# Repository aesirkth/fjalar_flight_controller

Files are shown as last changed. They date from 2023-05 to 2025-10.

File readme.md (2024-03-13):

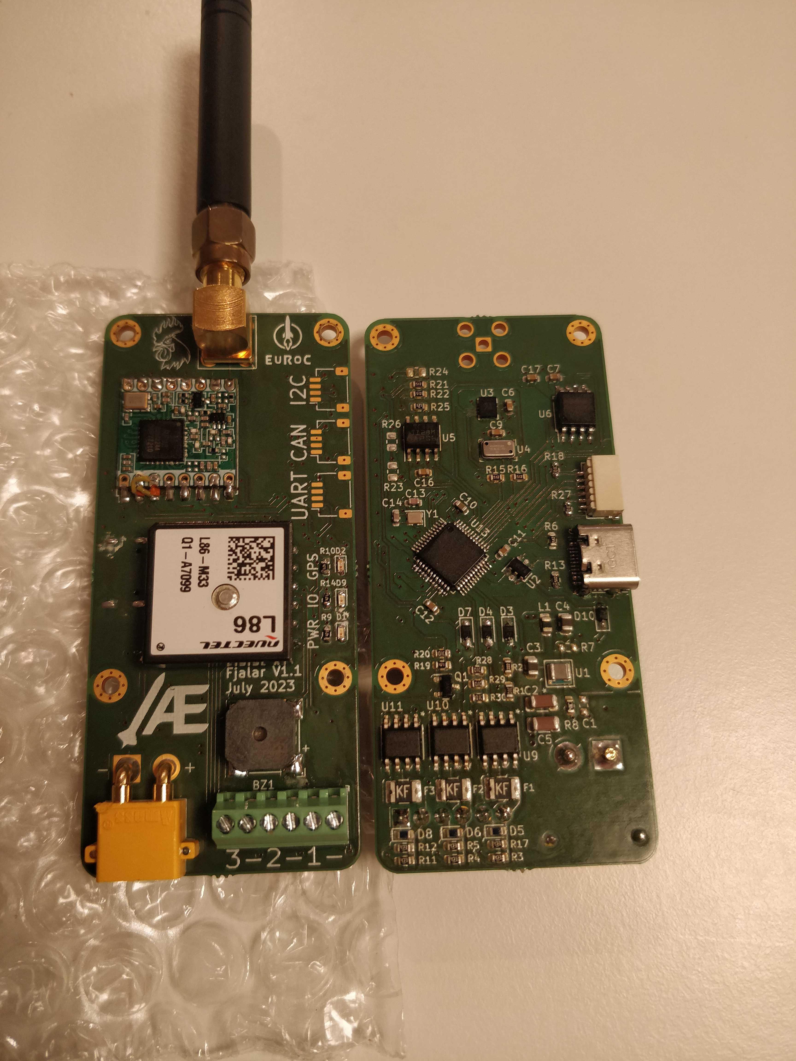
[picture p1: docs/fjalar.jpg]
fjalar


# Fjalar flight controller
Fjalar is a rooster in Jotunheim who heralds the advent of ragnarök, or in our case, apogee.

### features
1. 3 pyro channels
1. barometer
1. IMU
1. GPS
1. USB-C
1. flash memory
1. CAN, I2C, UART connectors
1. LoRa radio
1. continuity detection

### schematic
see [here](./design/euroc_controller.pdf)

### hardware
hopefully soon :)

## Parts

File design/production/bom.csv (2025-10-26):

Designator | Footprint | Quantity | Value | LCSC Part #
BZ1 | MagneticBuzzer_CUI_CMT-8504-100-SMT | 1 | CMT-8504-100
C1, C15, C2, C3, C8 | 0603 | 5 | 1u
C10, C11, C12 | 0603 | 3 | 4u7
C13, C14 | 0603 | 2 | 14p
C16, C17, C6, C7, C9 | 0603 | 5 | 0.1u
C18, C19 | 0603 | 2 | 10u
C20 | 0603 | 1 | 220n
C21, C4, C5 | 0603 | 3 | 100n
D1 | 0603 | 1 | power
D10 | D_SOD-323_HandSoldering | 1 | D_Small
D2 | 0603 | 1 | LED_FIX
D3, D4, D7 | D_SOD-323_HandSoldering | 3 | 3V
D5, D6, D8 | 0603 | 3 | 15V
D9 | 0603 | 1 | status
F1, F2, F3 | 1210 | 3 | Polyfuse
FB2, FB4 | 0805 | 2 | BLM18KG102SN1D
H1, H2, H3, H4 | MountingHole_2.2mm_M2_Pad_Via | 4 | MountingHole_Pad
IC1 | SOT-23-6_Handsoldering | 1 | LMR50410Y3
J1 | AMASS_XT30PW-M_1x02_P2.50mm_Horizontal | 1 | xt30
J2 | JST_GH_SM06B-GHS-TB_1x06-1MP_P1.25mm_Horizontal | 1 | jst gh 6
J3 | JST_GH_SM04B-GHS-TB_1x04-1MP_P1.25mm_Horizontal | 1 | jst gh 4
J6 | SMA_Amphenol_901-143_Horizontal | 1 | SMA
J7 | TerminalBlock_TE_282834-6_1x06_P2.54mm_Horizontal | 1 | Screw_Terminal_01x06
J8 | USB_C_Receptacle_Palconn_UTC16-G | 1 | USB_C_Receptacle_USB2.0
J9 | JST_SH_SM06B-SRSS-TB_1x06-1MP_P1.00mm_Horizontal | 1 | jst_sh 6
L2 | L_Wurth_WE-LQSH-3012 | 1 | 4.7u
Q1 | SOT-23 | 1 | MMBT3904
R1, R18, R20, R27, R28, R29, R30 | 0603 | 7 | 10k
R10, R14, R19, R9 | 0603 | 4 | 470
R11, R12, R17, R3, R4, R5 | 0603 | 6 | 3k
R13, R15, R16, R6 | 0603 | 4 | 5k1
R2 | 0603 | 1 | 2k2
R25 | 0603 | 1 | 120
SW1 | SW_SPST_B3U-1000P | 1 | SW_SPST
U10, U11, U9 | SOIC_050ASTR_STM | 3 | VN7050ASTR
U12 | HOPERF_RFM9XW_SMD | 1 | RFM98W-433S2
U13 | LQFP-48_7x7mm_P0.5mm | 1 | STM32U575CGTx
U2 | SOT-23-6 | 1 | USBLC6-2SC6
U3 | LGA-14_3x2.5mm_P0.5mm_LayoutBorder3x4y | 1 | LSM6DSO32
U4 | LGA-8_3x5mm_P1.25mm | 1 | MS5611-01BA
U5 | SOIC-8_3.9x4.9mm_P1.27mm | 1 | TCAN332
U6 | SOIC-8_5.23x5.23mm_P1.27mm | 1 | W25Q128JVS
U7 | LGA-12_2x2mm_P0.5mm | 1 | LIS2MDL
U8 | Quectel_L80-R | 1 | LC86
Y1 | Crystal_SMD_2016-4Pin_2.0x1.6mm | 1 | 48MHz

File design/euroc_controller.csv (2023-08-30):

Source: | /home/olof/programs/electronics/fjalar_controller/design/euroc_controller.kicad_sch
Date: | Thu 15 Jun 2023 06:48:31 PM CEST
Tool: | Eeschema 7.0.5
Generator: | /app/share/kicad/plugins/bom_csv_grouped_by_value.py
Component Count: | 85
Collated Components:
Item | Qty | Reference(s) | Value | LibPart | Footprint | Datasheet | DNP | Sim.Device | Sim.Pins
1 | 1 | BZ1 | CMT-8504-100 | Device:Buzzer | Buzzer_Beeper:MagneticBuzzer_CUI_CMT-8504-100-SMT | ~
2 | 5 | C1, C2, C10, C11, C12 | 4u7 | Device:C_Small | Capacitor_SMD:C_0603_1608Metric | ~
3 | 5 | C3, C4, C5, C8, C15 | 47u | Device:C_Small | Capacitor_SMD:C_0603_1608Metric | ~
4 | 5 | C6, C7, C9, C16, C17 | 0.1u | Device:C_Small | Capacitor_SMD:C_0603_1608Metric | ~
5 | 2 | C13, C14 | 22p | Device:C_Small | Capacitor_SMD:C_0603_1608Metric | ~
6 | 1 | D1 | power | Device:LED_Small | Diode_SMD:D_0603_1608Metric | ~
7 | 1 | D2 | LED_FIX | Device:LED_Small | Diode_SMD:D_0603_1608Metric | ~
8 | 3 | D3, D4, D7 | 3V | Device:D_Zener_Small | Diode_SMD:D_0603_1608Metric | ~
9 | 3 | D5, D6, D8 | 15V | Device:D_TVS | Diode_SMD:D_0603_1608Metric | ~
10 | 1 | D9 | status | Device:LED_Small | Diode_SMD:D_0603_1608Metric | ~
11 | 1 | D10 | D_Small | Device:D_Small | Diode_SMD:D_0603_1608Metric | ~ |  | D | 1=K 2=A
12 | 3 | F1, F2, F3 | Polyfuse | Device:Polyfuse | Fuse:Fuse_1210_3225Metric_Pad1.42x2.65mm_HandSolder | ~
13 | 4 | H1, H2, H3, H4 | MountingHole_Pad | Mechanical:MountingHole_Pad | MountingHole:MountingHole_2.2mm_M2_Pad_Via | ~
14 | 1 | J1 | xt30 | Connector:Barrel_Jack | Connector_AMASS:AMASS_XT30PW-M_1x02_P2.50mm_Horizontal | ~
15 | 3 | J2, J4, J5 | jst_sh 4 | Connector_Generic_MountingPin:Conn_01x04_MountingPin | Connector_JST:JST_SH_BM04B-SRSS-TB_1x04-1MP_P1.00mm_Vertical | ~
16 | 1 | J6 | SMA | Connector:Conn_Coaxial | Connector_Coaxial:SMA_Amphenol_901-143_Horizontal | ~
17 | 1 | J7 | Screw_Terminal_01x06 | Connector:Screw_Terminal_01x06 | TerminalBlock_TE-Connectivity:TerminalBlock_TE_282834-6_1x06_P2.54mm_Horizontal | ~
18 | 1 | J8 | USB_C_Receptacle_USB2.0 | Connector:USB_C_Receptacle_USB2.0 | Connector_USB:USB_C_Receptacle_Palconn_UTC16-G | https://www.usb.org/sites/default/files/documents/usb_type-c.zip
19 | 1 | J9 | jst_sh 4 | Connector_Generic_MountingPin:Conn_01x06_MountingPin | Connector_JST:JST_SH_SM06B-SRSS-TB_1x06-1MP_P1.00mm_Horizontal | ~
20 | 1 | L1 | L_Small | Device:L_Small | Inductor_SMD:L_0603_1608Metric | ~
21 | 1 | Q1 | MMBT3904 | Transistor_BJT:MMBT3904 | Package_TO_SOT_SMD:SOT-23 | https://www.onsemi.com/pub/Collateral/2N3903-D.PDF
22 | 5 | R1, R7, R18, R20, R27 | 10k | Device:R_Small | Resistor_SMD:R_0603_1608Metric | ~
23 | 1 | R2 | 2k2 | Device:R_Small | Resistor_SMD:R_0603_1608Metric | ~
24 | 6 | R3, R4, R5, R11, R12, R17 | 47k | Device:R_Small | Resistor_SMD:R_0603_1608Metric | ~
25 | 6 | R6, R13, R15, R16, R21, R22 | 5k1 | Device:R_Small | Resistor_SMD:R_0603_1608Metric | ~
26 | 1 | R8 | 4.3k | Device:R_Small | Resistor_SMD:R_0603_1608Metric | ~
27 | 4 | R9, R10, R14, R19 | 1k | Device:R_Small | Resistor_SMD:R_0603_1608Metric | ~
28 | 3 | R23, R24, R26 | 100 | Device:R_Small | Resistor_SMD:R_0805_2012Metric | ~
29 | 1 | R25 | 120 | Device:R_Small | Resistor_SMD:R_0603_1608Metric | ~
30 | 1 | U1 | TPSM5601R5 | Converter_DCDC:TPSM53602RDA | Package_DFN_QFN:Texas_B3QFN-14-1EP_5x5.5mm_P0.65mm | https://www.ti.com/lit/ds/symlink/tpsm53602.pdf
31 | 1 | U2 | USBLC6-2SC6 | Power_Protection:USBLC6-2SC6 | Package_TO_SOT_SMD:SOT-23-6 | https://www.st.com/resource/en/datasheet/usblc6-2.pdf
32 | 1 | U3 | LSM6DSO32 | Sensor_Motion:LSM6DS3 | Package_LGA:LGA-14_3x2.5mm_P0.5mm_LayoutBorder3x4y | https://www.st.com/resource/en/datasheet/lsm6ds3tr-c.pdf
33 | 1 | U4 | MS5611-01BA | Sensor_Pressure:MS5611-01BA | Package_LGA:LGA-8_3x5mm_P1.25mm | https://www.te.com/commerce/DocumentDelivery/DDEController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
34 | 1 | U5 | TCAN332 | Interface_CAN_LIN:TCAN332 | Package_SO:SOIC-8_3.9x4.9mm_P1.27mm | http://www.ti.com/lit/ds/symlink/tcan337.pdf
35 | 1 | U6 | W25Q128JVS | Memory_Flash:W25Q128JVS | Package_SO:SOIC-8_5.23x5.23mm_P1.27mm | http://www.winbond.com/resource-files/w25q128jv_dtr%20revc%2003272018%20plus.pdf
36 | 1 | U7 | RFM69W | RF_Module:RFM69W | RF_Module:HOPERF_RFM69HW | https://www.hoperf.com/data/upload/portal/20181127/5bfcbe34756e1.pdf
37 | 1 | U8 | L86 | RF_GPS:L80-R | RF_GPS:Quectel_L80-R | https://www.quectel.com/UploadImage/Downlad/Quectel_L80-R_Hardware_Design_V1.2.pdf
38 | 3 | U9, U10, U11 | VN7050ASTR | VN7050AS:VN7050ASTR | lib:SOIC_050ASTR_STM | VN7050ASTR
39 | 1 | U13 | STM32U575CGTx | MCU_ST_STM32U5:STM32U575CGTx | Package_QFP:LQFP-48_7x7mm_P0.5mm | https://www.st.com/resource/en/datasheet/stm32u575cg.pdf
40 | 1 | Y1 | 48MHz | Device:Crystal_GND24 | Crystal:Crystal_SMD_2016-4Pin_2.0x1.6mm | ~

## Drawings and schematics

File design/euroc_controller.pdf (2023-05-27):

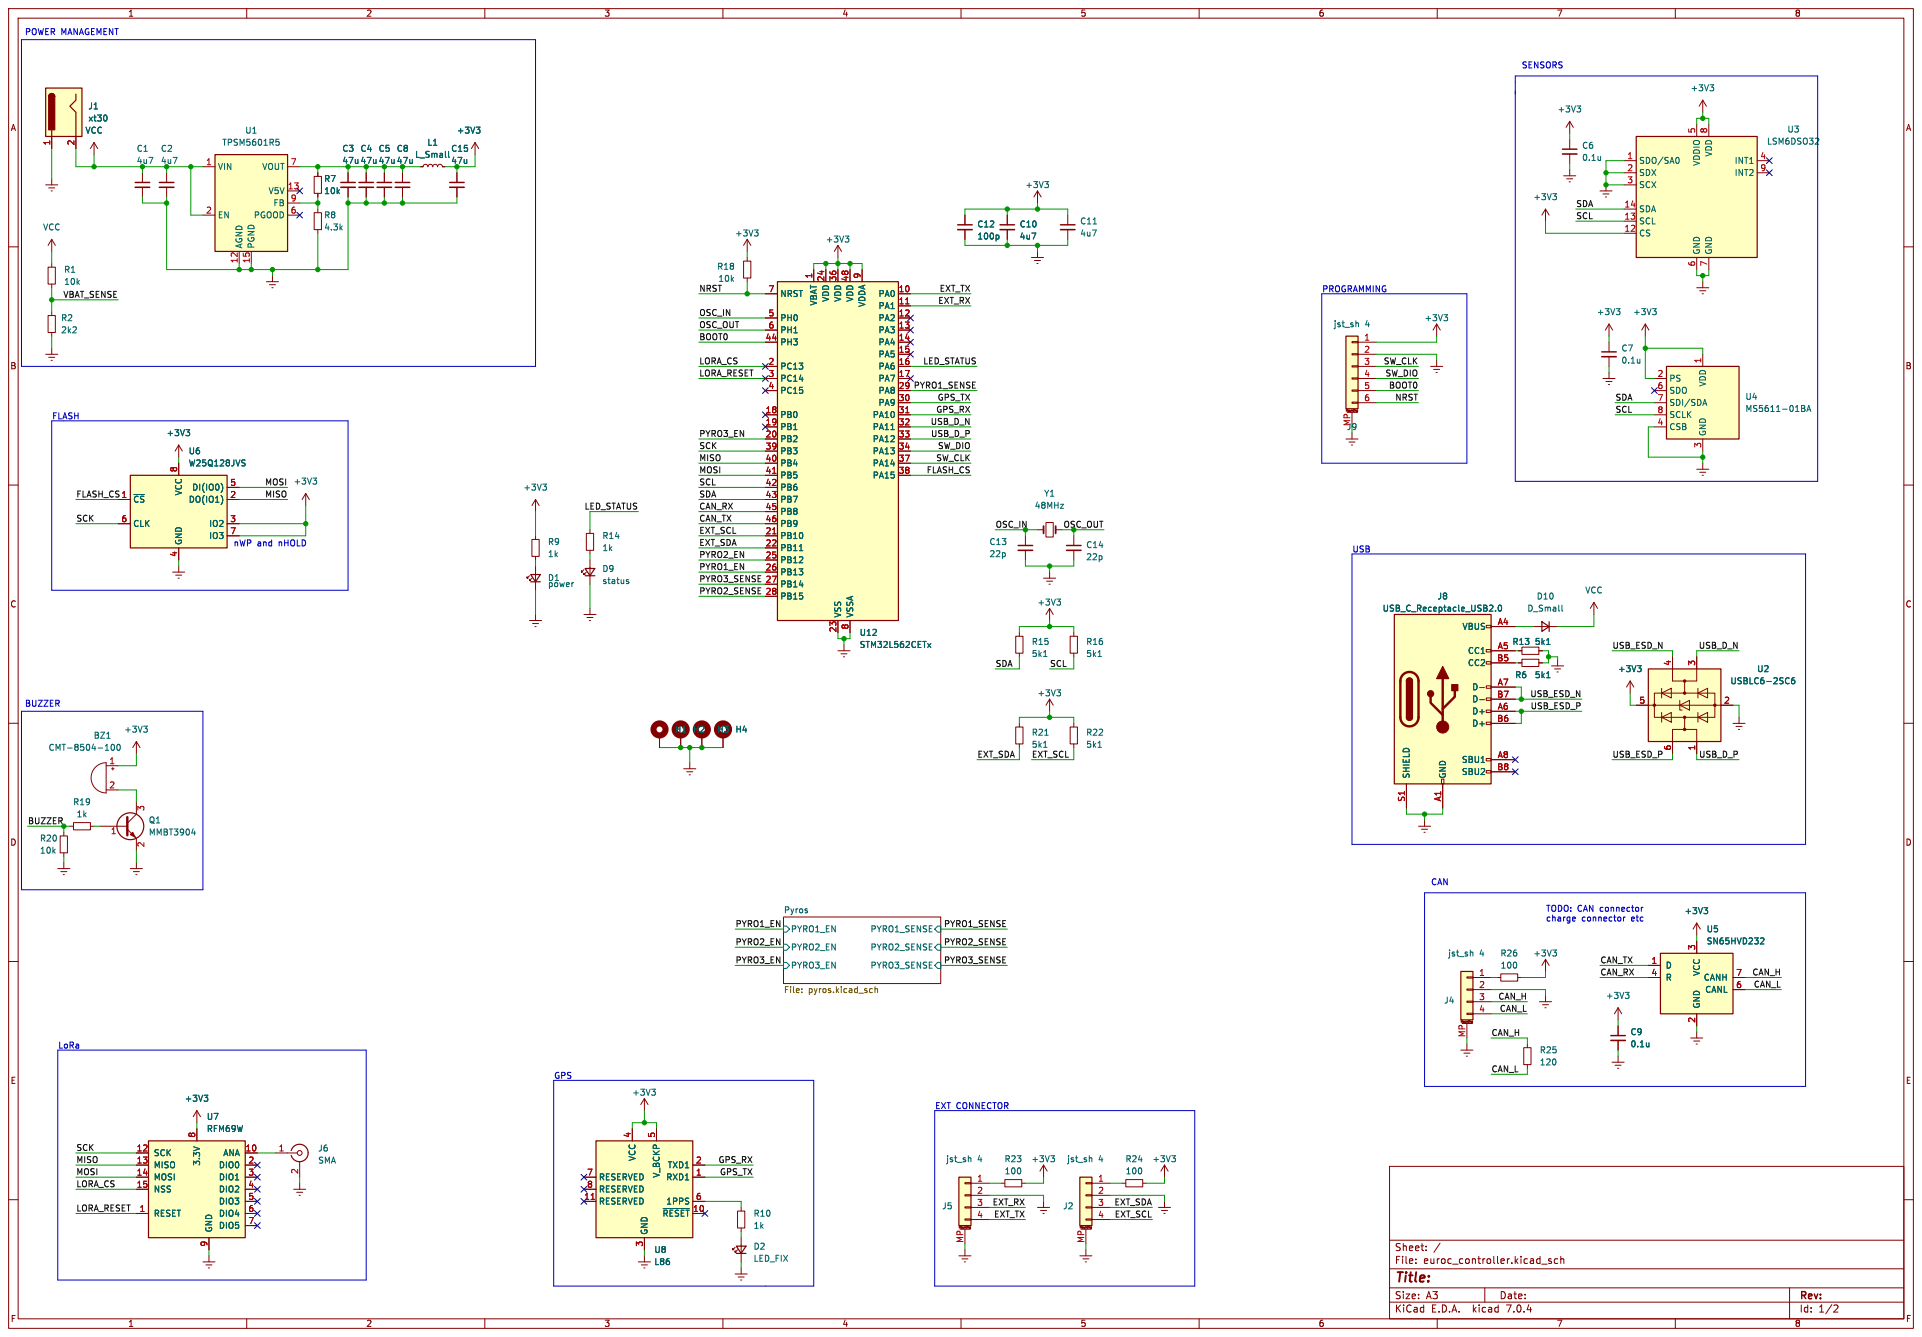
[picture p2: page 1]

1 PA0 10 PA1 11 PA2 12 PA3 13 PA4 14 PA5 15 PA6 16 PA7 17 PB0 18 PB1 19 PC13 2 PB2 20 PB10 21 PB11 22 VSS 23 VDD 24 PB12 25 PB13 26 PB14 27 PB15 28 PA8 29 PC14 3 PA9 30 PA10 31 PA11 32 PA12 33 PA13 34 VDD 36 PA14 37 PA15 38 PB3 39 PC15 4 PB4 40 PB5 41 PB6 42 PB7 43 PH3 44 PB8 45 PB9 46 VDD 48 PH0 5 PH1 6 NRST 7 VSSA

Pyros File: pyros.kicad_sch
Id: 1/2 Title: File: euroc_controller.kicad_sch Sheet: / PYRO1_EN
PYRO2_EN

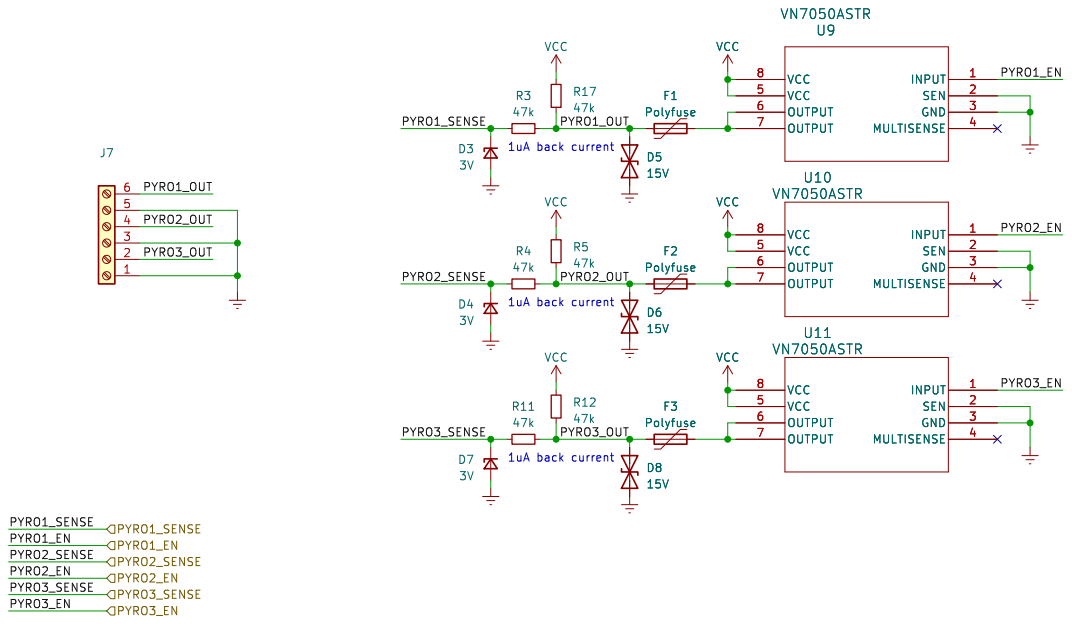
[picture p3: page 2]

Id: 2/2 Title: File: pyros.kicad_sch Sheet: /Pyros/

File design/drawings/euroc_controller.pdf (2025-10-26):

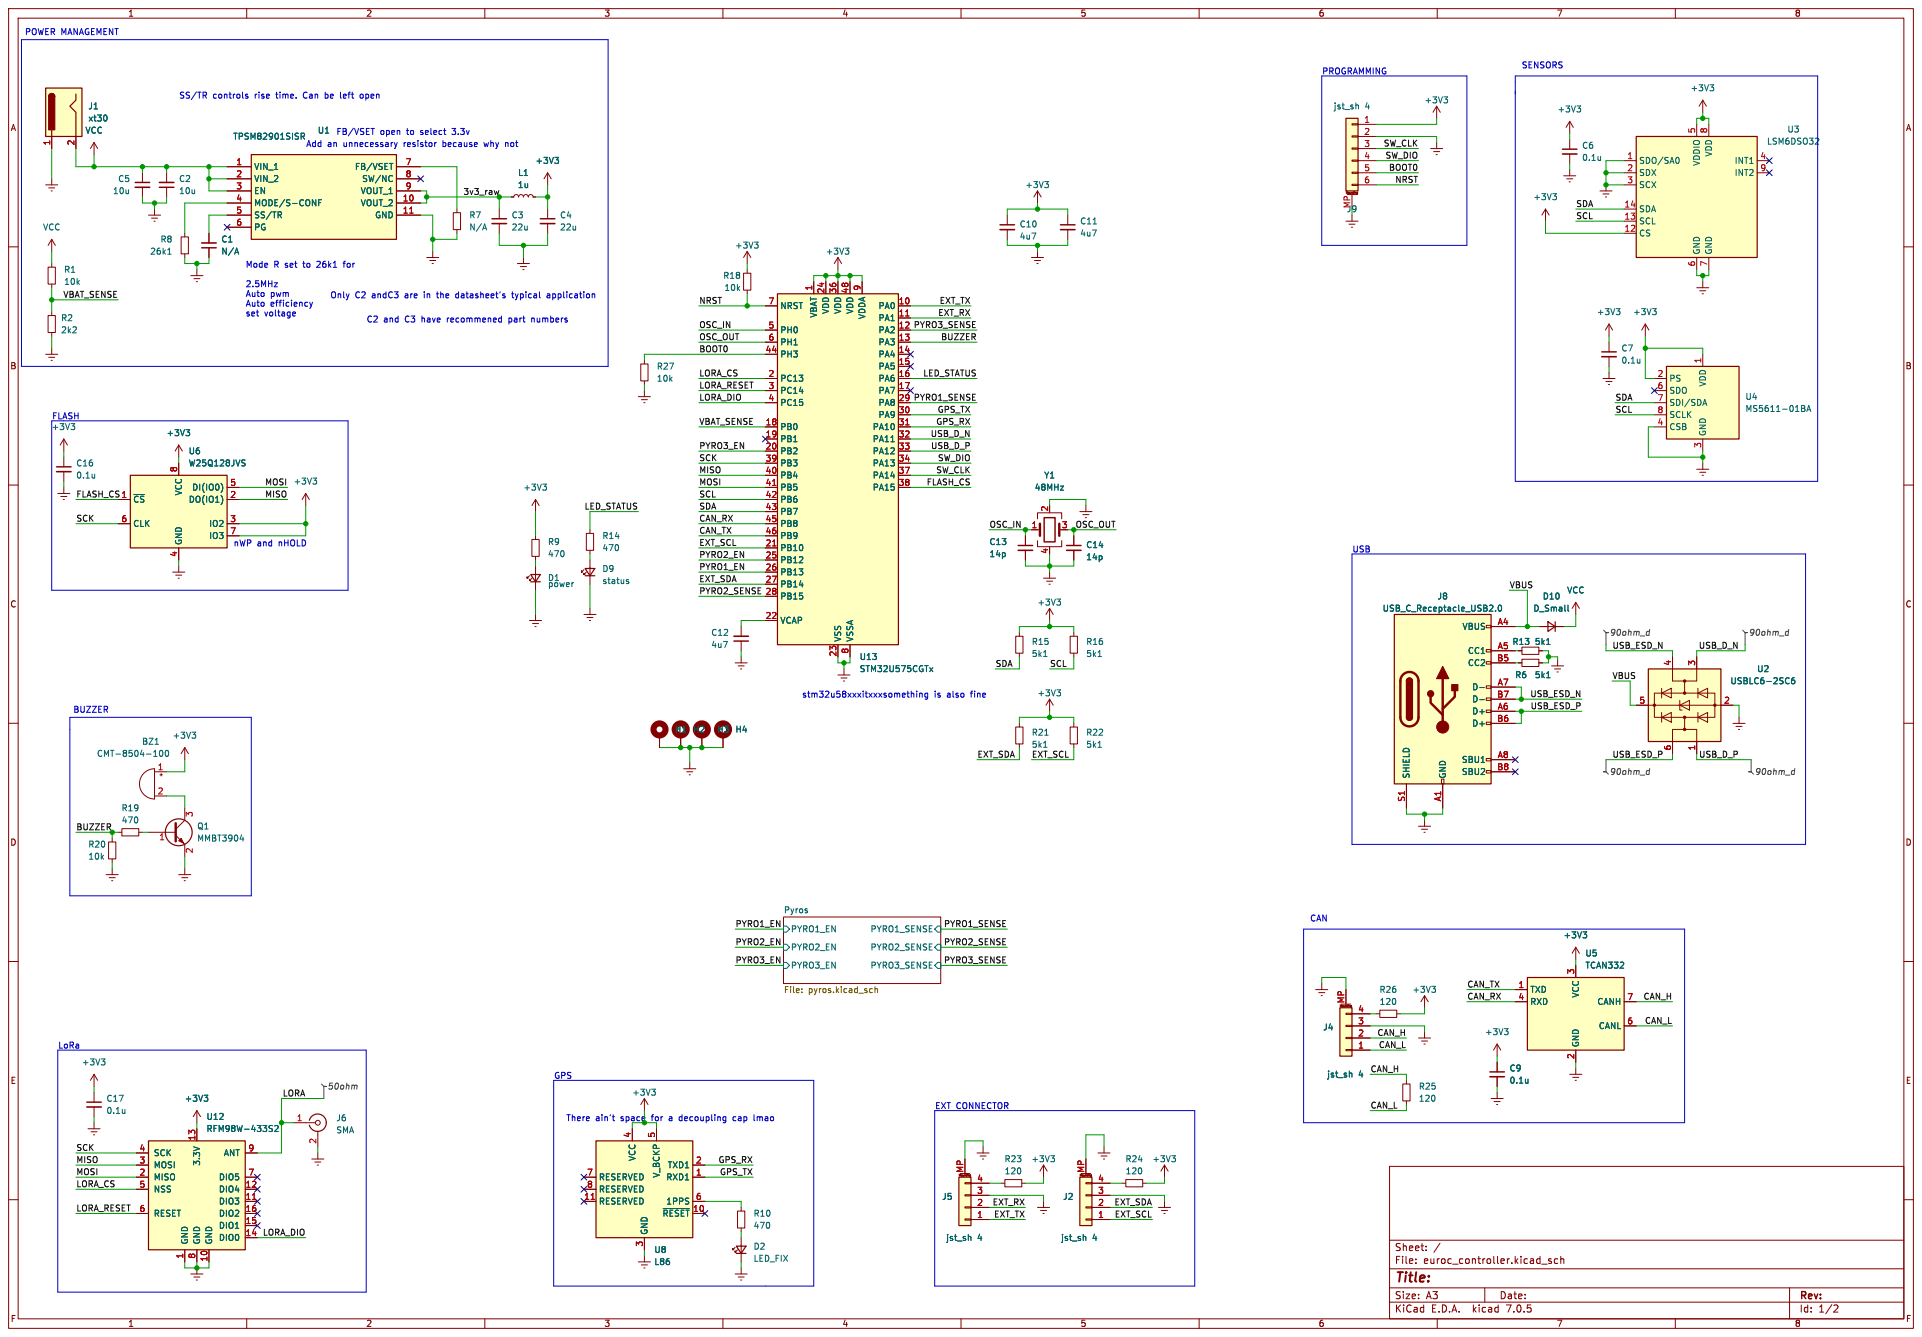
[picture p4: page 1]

SDO/SA0 1 CS 12 SCL 13 SDA 14 SDX 2 SCX 3

1 PA0 10 PA1 11 PA2 12 PA3 13 PA4 14 PA5 15 PA6 16 PA7 17 PB0 18 PB1 19 PC13 2 PB2 20 PB10 21 VCAP 22 VSS 23 VDD 24 PB12 25 PB13 26 PB14 27 PB15 28 PA8 29 PC14 3 PA9 30 PA10 31 PA11 32 PA12 33 PA13 34 VDD 36 PA14 37 PA15 38 PB3 39 PC15 4 PB4 40 PB5 41 PB6 42 PB7 43 PH3 44 PB8 45 PB9 46 VDD 48 PH0 5 PH1 6 NRST 7 VSSA

6 U2 USBLC6-2SC6 VCC GND A1 VBUS A4 CC1 A5 D+ A6 D- A7 SBU1 A8 CC2 B5 D+ B6 D- B7 SBU2 B8 SHIELD S1

Pyros File: pyros.kicad_sch GND

Id: 1/2 Title: File: euroc_controller.kicad_sch Sheet: / PYRO1_EN
PYRO2_EN

1 GND 10 DIO3 11 DIO4 12 3.3V 13 DIO0 14 DIO1 15 DIO2 16 MISO 2 MOSI 3 SCK 4 NSS 5 RESET 6 DIO5 7 GND

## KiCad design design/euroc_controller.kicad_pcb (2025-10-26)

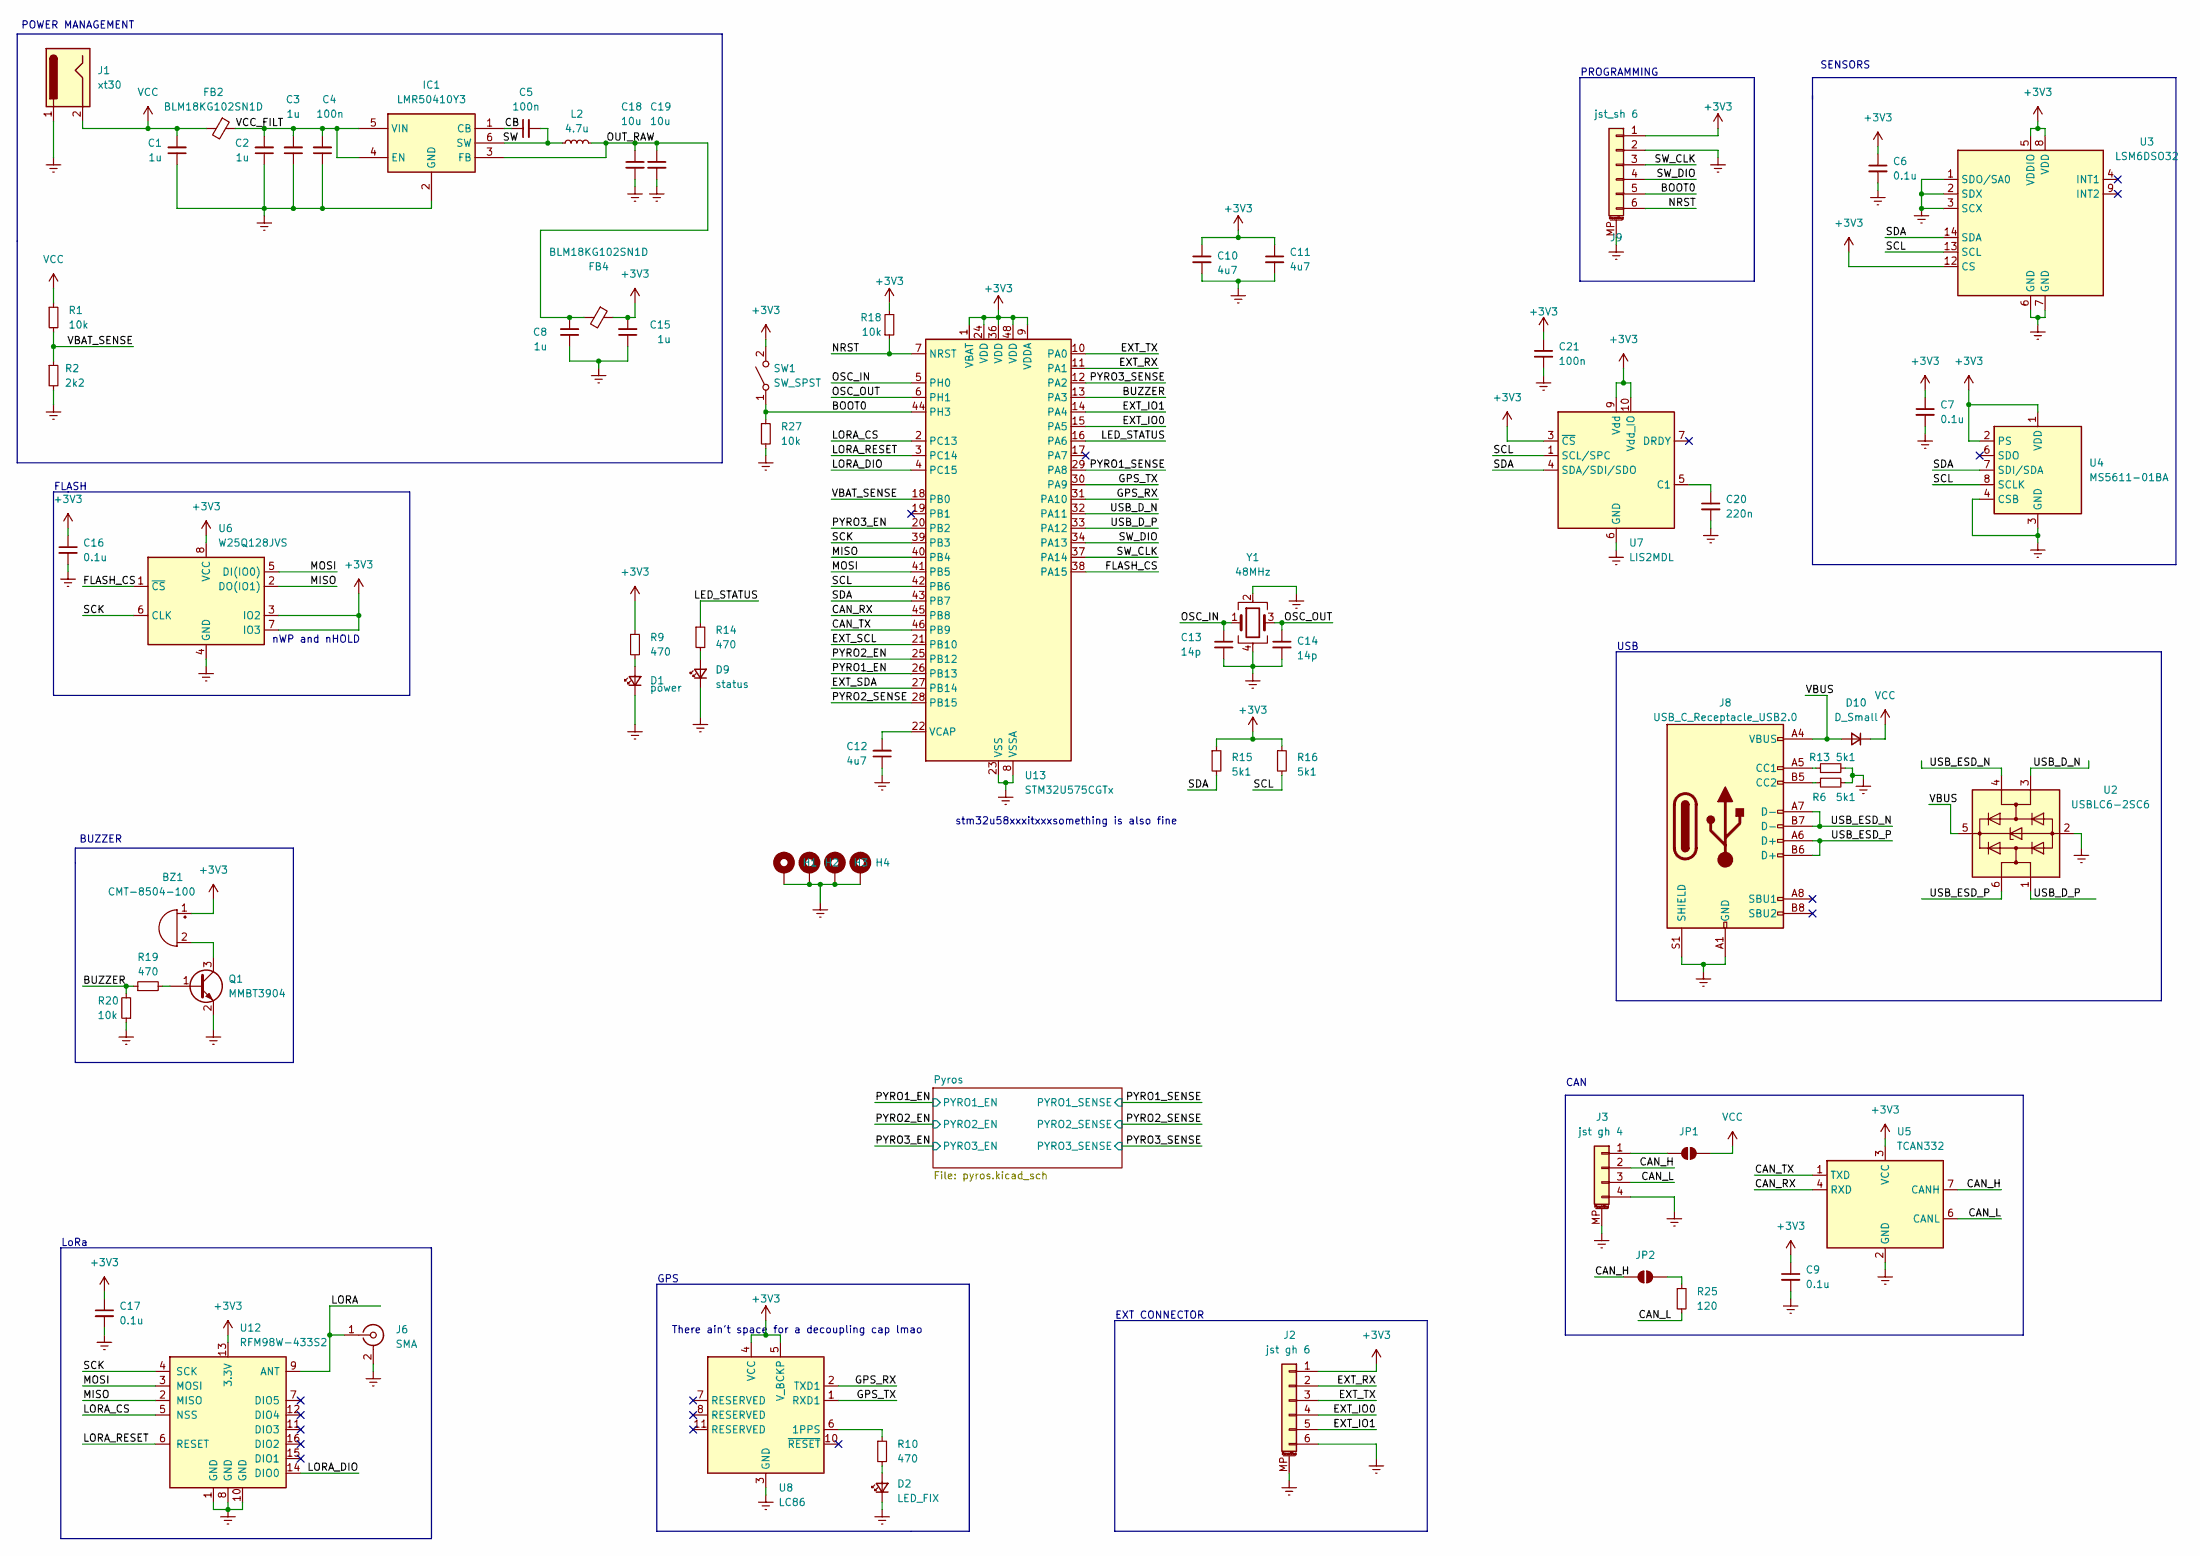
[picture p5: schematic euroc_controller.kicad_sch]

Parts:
BZ1: CMT-8504-100; MagneticBuzzer_CUI_CMT-8504-100-SMT
C1, C2, C3, C8, C15: 1u; C_0603_1608Metric
C4, C5, C21: 100n; C_0603_1608Metric
C6, C7, C9, C16, C17: 0.1u; C_0603_1608Metric
C10, C11, C12: 4u7; C_0603_1608Metric
C13, C14: 14p; C_0603_1608Metric
C18, C19: 10u; C_0603_1608Metric
C20: 220n; C_0603_1608Metric
D1: power; D_0603_1608Metric
D2: LED_FIX; D_0603_1608Metric
D9: status; D_0603_1608Metric
D10: D_Small; D_SOD-323_HandSoldering
FB2, FB4: BLM18KG102SN1D; L_0805_2012Metric_Pad1.15x1.40mm_HandSolder
H1, H2, H3, H4: MountingHole_Pad; MountingHole_2.2mm_M2_Pad_Via
IC1: LMR50410Y3; SOT-23-6_Handsoldering; Mouser Part Number 595-LMR50410YQDBVRQ1
J1: xt30; AMASS_XT30PW-M_1x02_P2.50mm_Horizontal
J2: jst gh 6; JST_GH_SM06B-GHS-TB_1x06-1MP_P1.25mm_Horizontal
J3: jst gh 4; JST_GH_SM04B-GHS-TB_1x04-1MP_P1.25mm_Horizontal
J6: SMA; SMA_Amphenol_901-143_Horizontal
J8: USB_C_Receptacle_USB2.0; USB_C_Receptacle_Palconn_UTC16-G
J9: jst_sh 6; JST_SH_SM06B-SRSS-TB_1x06-1MP_P1.00mm_Horizontal
JP1, JP2: SolderJumper_2_Open; SolderJumper-2_P1.3mm_Open_TrianglePad1.0x1.5mm
L2: 4.7u; L_Wurth_WE-LQSH-3012
Q1: MMBT3904; SOT-23
R1, R18, R20, R27: 10k; R_0603_1608Metric
R2: 2k2; R_0603_1608Metric
R6, R13, R15, R16: 5k1; R_0603_1608Metric
R9, R10, R14, R19: 470; R_0603_1608Metric
R25: 120; R_0603_1608Metric
SW1: SW_SPST; SW_SPST_B3U-1000P
U2: USBLC6-2SC6; SOT-23-6
U3: LSM6DSO32; LGA-14_3x2.5mm_P0.5mm_LayoutBorder3x4y
U4: MS5611-01BA; LGA-8_3x5mm_P1.25mm
U5: TCAN332; SOIC-8_3.9x4.9mm_P1.27mm
U6: W25Q128JVS; SOIC-8_5.23x5.23mm_P1.27mm
U7: LIS2MDL; LGA-12_2x2mm_P0.5mm
U8: LC86; Quectel_L80-R
U12: RFM98W-433S2; HOPERF_RFM9XW_SMD
U13: STM32U575CGTx; LQFP-48_7x7mm_P0.5mm
Y1: 48MHz; Crystal_SMD_2016-4Pin_2.0x1.6mm

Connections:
+3V3: BZ1.1 (-), C6.1, C7.1, C9.1, C10.1, C11.1, C15.2, C16.1, C17.1, C21.1, FB4.1, J2.1, J9.1, R9.1, R15.1, R16.1, R18.2, SW1.2 (B), U3.5 (VDDIO), U3.8 (VDD), U3.12 (CS), U4.1 (VDD), U4.2 (PS), U5.3 (VCC), U6.3 (IO2), U6.7 (IO3), U6.8 (VCC), U7.3 (~CS), U7.9 (Vdd), U7.10 (Vdd_IO), U8.4 (VCC), U8.5 (V_BCKP), U12.13 (3.3V), U13.1 (VBAT), U13.9 (VDDA), U13.24 (VDD), U13.36 (VDD), U13.48 (VDD)
/BOOT0: J9.5, R27.1, SW1.1 (A), U13.44 (PH3)
/BUZZER: R19.1, R20.2, U13.13 (PA3)
/CAN_H: J3.2, JP2.2 (B), U5.7 (CANH)
/CAN_L: J3.3, R25.2, U5.6 (CANL)
/CAN_RX: U5.4 (RXD), U13.45 (PB8)
/CAN_TX: U5.1 (TXD), U13.46 (PB9)
/CB: C5.1, IC1.1 (CB)
/EXT_IO0: J2.4, U13.15 (PA5)
/EXT_IO1: J2.5, U13.14 (PA4)
/EXT_RX: J2.2, U13.11 (PA1)
/EXT_SCL: U13.21 (PB10)
/EXT_SDA: U13.27 (PB14)
/EXT_TX: J2.3, U13.10 (PA0)
/FLASH_CS: U6.1 (~CS), U13.38 (PA15)
/GPS_RX: U8.2 (TXD1), U13.31 (PA10)
/GPS_TX: U8.1 (RXD1), U13.30 (PA9)
/LED_STATUS: R14.1, U13.16 (PA6)
/LORA: J6.1 (In), U12.9 (ANT)
/LORA_CS: U12.5 (NSS), U13.2 (PC13)
/LORA_DIO: U12.14 (DIO0), U13.4 (PC15)
/LORA_RESET: U12.6 (RESET), U13.3 (PC14)
/MISO: U6.2 (DO(IO1)), U12.2 (MISO), U13.40 (PB4)
/MOSI: U6.5 (DI(IO0)), U12.3 (MOSI), U13.41 (PB5)
/NRST: J9.6, R18.1, U13.7 (NRST)
/OSC_IN: C13.1, U13.5 (PH0), Y1.1
/OSC_OUT: C14.1, U13.6 (PH1), Y1.3
/OUT_RAW: C8.2, C18.1, C19.1, FB4.2, IC1.3 (FB), L2.2
/PYRO1_EN: U13.26 (PB13); also elsewhere on the board
/PYRO1_SENSE: U13.29 (PA8); also elsewhere on the board
/PYRO2_EN: U13.25 (PB12); also elsewhere on the board
/PYRO2_SENSE: U13.28 (PB15); also elsewhere on the board
/PYRO3_EN: U13.20 (PB2); also elsewhere on the board
/PYRO3_SENSE: U13.12 (PA2); also elsewhere on the board
/SCK: U6.6 (CLK), U12.4 (SCK), U13.39 (PB3)
/SCL: R16.2, U3.13 (SCL), U4.8 (SCLK), U7.1 (SCL/SPC), U13.42 (PB6)
/SDA: R15.2, U3.14 (SDA), U4.7 (SDI/SDA), U7.4 (SDA/SDI/SDO), U13.43 (PB7)
/SW: C5.2, IC1.6 (SW), L2.1
/SW_CLK: J9.3, U13.37 (PA14)
/SW_DIO: J9.4, U13.34 (PA13)
/USB_D_N: U2.3 (I/O2), U13.32 (PA11)
/USB_D_P: U2.1 (I/O1), U13.33 (PA12)
/USB_ESD_N: J8.A7 (D-), J8.B7 (D-), U2.4 (I/O2)
/USB_ESD_P: J8.A6 (D+), J8.B6 (D+), U2.6 (I/O1)
/VBAT_SENSE: R1.2, R2.1, U13.18 (PB0)
/VBUS: D10.2 (A), J8.A4 (VBUS), J8.A9 (VBUS), J8.B4 (VBUS), J8.B9 (VBUS), U2.5 (VBUS)
/VCC_FILT: C2.2, C3.2, C4.2, FB2.1, IC1.4 (EN), IC1.5 (VIN)
Earth: C1.1, C2.1, C3.1, C4.1, C6.2, C7.2, C8.1, C9.2, C10.2, C11.2, C12.1, C13.2, C14.2, C15.1, C16.2, C17.2, C18.2, C19.2, C20.2, C21.2, D1.1 (K), D2.1 (K), D9.1 (K), H1.1, H2.1, H3.1, H4.1, IC1.2 (GND), J1.1, J2.6, J2.MP (MountPin), J3.4, J3.MP (MountPin), J6.2 (Ext), J8.A1 (GND), J8.A12 (GND), J8.B1 (GND), J8.B12 (GND), J8.S1 (SHIELD), J9.2, J9.MP (MountPin), Q1.2 (E), R2.2, R6.2, R13.2, R20.1, R27.2, U2.2 (GND), U3.1 (SDO/SA0), U3.2 (SDX), U3.3 (SCX), U3.6 (GND), U3.7 (GND), U4.3 (GND), U4.4 (CSB), U4.5 (CSB), U5.2 (GND), U6.4 (GND), U7.6 (GND), U7.8 (GND), U8.3 (GND), U8.12 (GND), U12.1 (GND), U12.8 (GND), U12.10 (GND), U13.8 (VSSA), U13.23 (VSS), U13.35 (VSS), U13.47 (VSS), Y1.2, Y1.4; also elsewhere on the board
unnamed: BZ1.2 (+), Q1.3 (C)
unnamed: D1.2 (A), R9.2
unnamed: D2.2 (A), R10.2
unnamed: D9.2 (A), R14.2
unnamed: J3.1, JP1.2 (B)
unnamed: J8.A5 (CC1), R13.1
unnamed: J8.B5 (CC2), R6.1
unnamed: JP2.1 (A), R25.1
unnamed: Q1.1 (B), R19.2
unnamed: C20.1, U7.5 (C1)
unnamed: R10.1, U8.6 (1PPS)
unnamed: C12.2, U13.22 (VCAP)
VCC: C1.2, D10.1 (K), FB2.2, J1.2, JP1.1 (A), R1.1; also elsewhere on the board

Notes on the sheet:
GPS
POWER MANAGEMENT
nWP and nHOLD
USB
FLASH
BUZZER
There ain't space for a decoupling cap lmao
SENSORS
PROGRAMMING
LoRa
stm32u58xxxitxxxsomething is also fine
EXT CONNECTOR
CAN

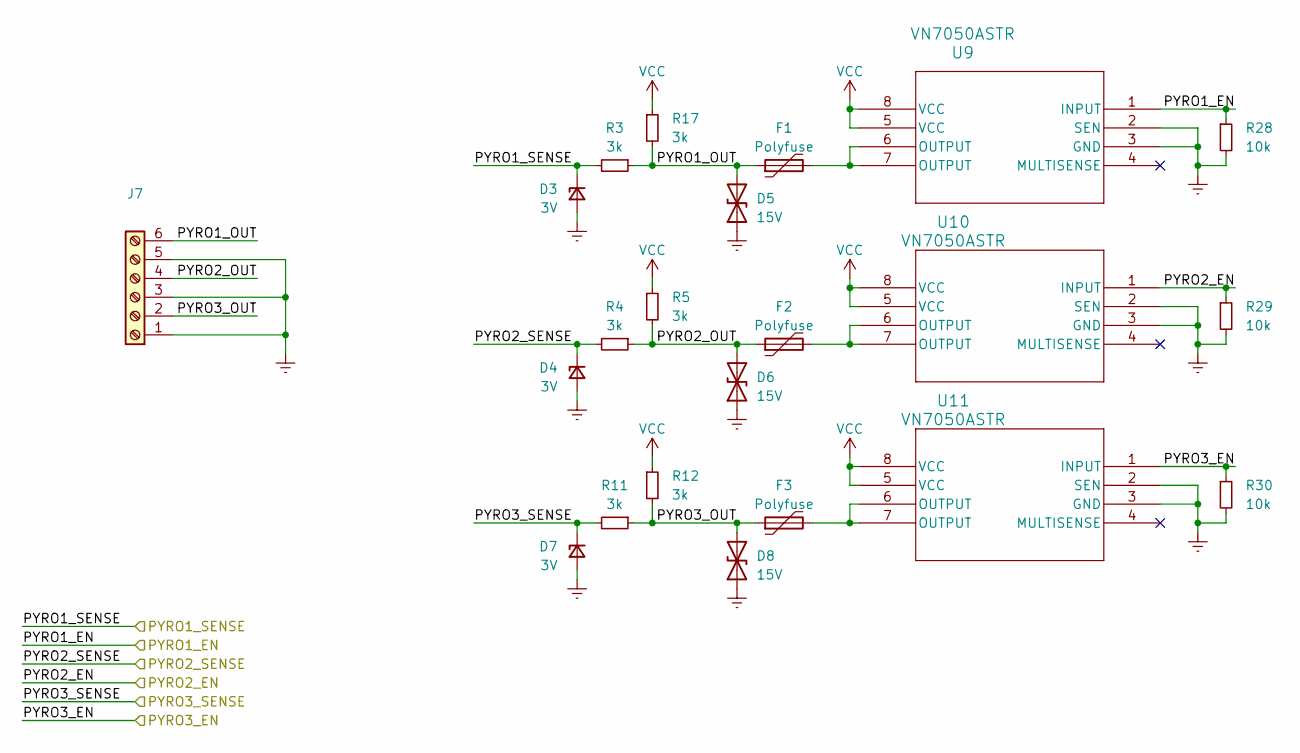
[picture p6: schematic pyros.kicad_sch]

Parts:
D3, D4, D7: 3V; D_SOD-323_HandSoldering
D5, D6, D8: 15V; D_0603_1608Metric
F1, F2, F3: Polyfuse; Fuse_1210_3225Metric_Pad1.42x2.65mm_HandSolder
J7: Screw_Terminal_01x06; TerminalBlock_TE_282834-6_1x06_P2.54mm_Horizontal
R3, R4, R5, R11, R12, R17: 3k; R_0603_1608Metric
R28, R29, R30: 10k; R_0603_1608Metric
U9, U10, U11: VN7050ASTR; SOIC_050ASTR_STM

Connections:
/PYRO1_EN: R28.1, U9.1 (INPUT); also elsewhere on the board
/PYRO1_SENSE: D3.1 (K), R3.2; also elsewhere on the board
/PYRO2_EN: R29.1, U10.1 (INPUT); also elsewhere on the board
/PYRO2_SENSE: D4.1 (K), R4.2; also elsewhere on the board
/PYRO3_EN: R30.1, U11.1 (INPUT); also elsewhere on the board
/PYRO3_SENSE: D7.1 (K), R11.2; also elsewhere on the board
/Pyros/PYRO1_OUT: D5.2 (A2), F1.1, J7.6, R3.1, R17.2
/Pyros/PYRO2_OUT: D6.2 (A2), F2.1, J7.4, R4.1, R5.2
/Pyros/PYRO3_OUT: D8.2 (A2), F3.1, J7.2, R11.1, R12.2
Earth: D3.2 (A), D4.2 (A), D5.1 (A1), D6.1 (A1), D7.2 (A), D8.1 (A1), J7.1, J7.3, J7.5, R28.2, R29.2, R30.2, U9.2 (SEN), U9.3 (GND), U10.2 (SEN), U10.3 (GND), U11.2 (SEN), U11.3 (GND); also elsewhere on the board
unnamed: F1.2, U9.6 (OUTPUT), U9.7 (OUTPUT)
unnamed: F2.2, U10.6 (OUTPUT), U10.7 (OUTPUT)
unnamed: F3.2, U11.6 (OUTPUT), U11.7 (OUTPUT)
VCC: R5.1, R12.1, R17.1, U9.5 (VCC), U9.8 (VCC), U10.5 (VCC), U10.8 (VCC), U11.5 (VCC), U11.8 (VCC); also elsewhere on the board

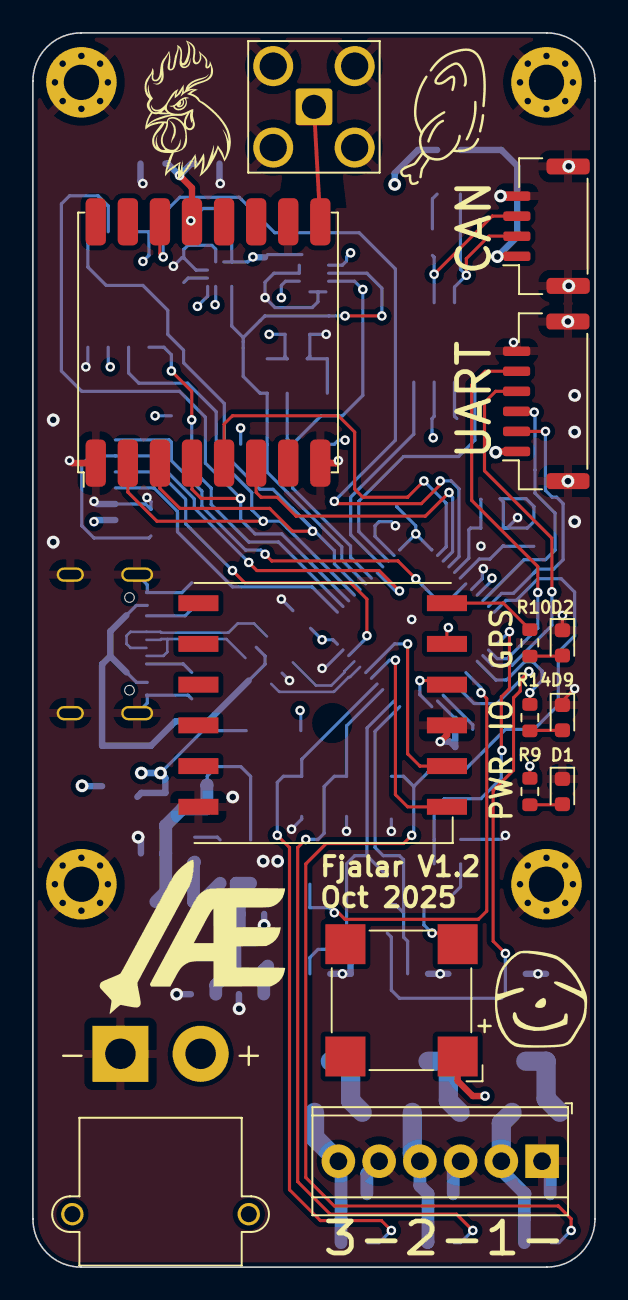
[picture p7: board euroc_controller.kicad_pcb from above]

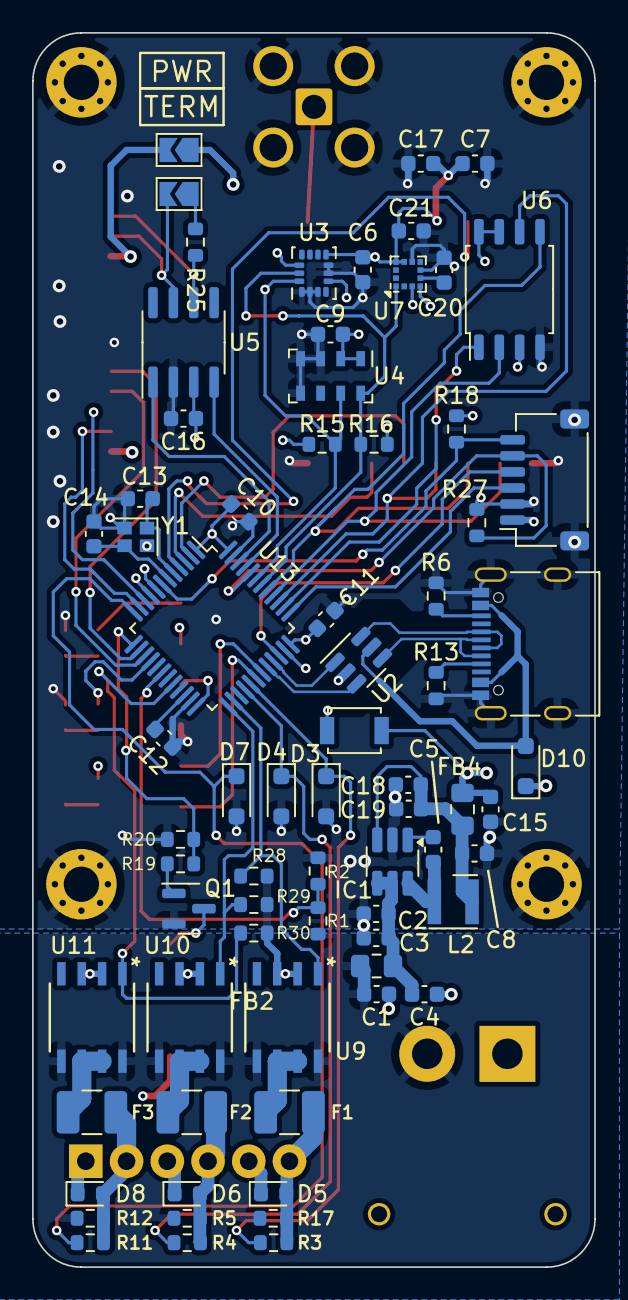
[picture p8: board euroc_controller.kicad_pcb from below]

Board: 4 copper layers, 35.1 x 77.0 mm, 90 parts (72 on the bottom side), 65 nets.

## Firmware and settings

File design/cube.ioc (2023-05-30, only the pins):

Mcu.UserName=STM32L562CETx
PA0.Signal=UART4_TX
PA1.Signal=UART4_RX
PA10.GPIO_Label=GPS_RX
PA10.Signal=USART1_RX
PA11.Signal=USB_DM
PA12.Signal=USB_DP
PA3.Signal=S_TIM2_CH4
PA6.GPIO_Label=LED_STATUS
PA6.Signal=GPIO_Output
PA8.GPIO_Label=PYRO1_SENSE
PA8.Signal=GPIO_Input
PA9.GPIO_Label=GPS_TX
PA9.Signal=USART1_TX
PB0.GPIO_Label=VBAT_SENSE
PB0.Signal=ADCx_IN15
PB10.Signal=I2C2_SCL
PB11.Signal=I2C2_SDA
PB12.GPIO_Label=PYRO2_EN
PB12.Signal=GPIO_Output
PB13.GPIO_Label=PYRO1_EN
PB13.Signal=GPIO_Output
PB14.GPIO_Label=PYRO3_SENSE
PB14.Signal=GPIO_Input
PB15.GPIO_Label=PYRO2_SENSE
PB15.Signal=GPIO_Input
PB2.GPIO_Label=PYRO3_EN
PB2.Signal=GPIO_Output
PB5.Signal=SPI1_MOSI
PB6.Signal=I2C1_SCL
PB7.Signal=I2C1_SDA
PB8.Signal=FDCAN1_RX
PB9.Signal=FDCAN1_TX
PC13.GPIO_Label=LORA_CS
PC13.Signal=GPIO_Output

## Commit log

2023-05-27 better structure
    [euroc_controller.kicad_pcb, euroc_controller.kicad_sch, pyros.kicad_sch]
2023-05-27 align mounting holes
    [euroc_controller.kicad_pcb, euroc_controller.kicad_sch]
2023-05-27 use real clock, fix esd vbus
    [euroc_controller.kicad_pcb, euroc_controller.kicad_sch]
2023-05-30 update ioc, add logo
    [euroc_controller.kicad_pcb, euroc_controller.kicad_sch]
2023-05-30 oof new umc (st32u5)
    [euroc_controller.kicad_pcb, euroc_controller.kicad_sch]
2023-05-30 fix new umc...
    [euroc_controller.kicad_sch]
2023-05-30 can transceiver, decoupling caps
    [euroc_controller.kicad_pcb, euroc_controller.kicad_sch]
2023-05-31 fix aesir logo
    [euroc_controller.kicad_pcb, euroc_controller.kicad_sch]
2023-05-31 better sma
    [euroc_controller.kicad_pcb, euroc_controller.kicad_sch]
2023-06-15 route dp
    [euroc_controller.kicad_pcb, euroc_controller.kicad_sch]
2023-06-15 redo for aisler
    [euroc_controller.kicad_pcb, euroc_controller.kicad_sch]
2023-07-15 PCB 1.1 old regulator
    [euroc_controller.kicad_pcb, euroc_controller.kicad_sch, pyros.kicad_sch]
2023-08-02 virtual environment working
    [baro.csv, imu.csv]
2023-08-02 PCB v1.1
    [euroc_controller.kicad_pcb, euroc_controller.kicad_sch, pyros.kicad_sch]
2023-08-30 remove firmware
    [baro.csv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]
